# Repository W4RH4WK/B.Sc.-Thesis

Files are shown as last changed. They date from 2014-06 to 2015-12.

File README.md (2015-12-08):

# Improved On-Board Communication for Low-Cost Mobile Robots

This project seeks to improve the communication process between the host
computer of an existing, low-cost robot, and some on-board peripherals. This
robot is used by the department of Computer Science at University of Innsbruck
for teaching students autonomous systems. The robot is driven by an Android
phone which communicates with the robot’s internal peripherals. The components
in use for this communication process introduce various problems which are
resolved by this project to ensure better user experience.

Possible prototypes have been evaluated to find the best possible solution for
the task. Although the best solution still has some flaws, another prototype
was created which brings some new benefits along. Among them are easy to use
and easy to maintain interfaces. Together with the prototypes documentation and
examples have been crafted to ensure easy access to the material for students.
Modularity of the robot has been improved which enables other people to easily
enhance the robots capabilities.

The component used in the final solution consists of a microcontroller which is
programmed to read in data from an Android phone and controls the robot
accordingly. Apart from hardware the microcontroller’s firmware has been
written together with and example Android application.

## Known Issues

- `2015-04-30` Since the firmware's command buffer logic ignores `\r` (carriage
  return) and terminates on `\n` (linefeed), one cannot use the corresponding
  values as arguments. Just increment the value by one before sending, you
  won't notice the difference anyway.

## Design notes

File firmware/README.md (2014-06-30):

# FT232 AVR Program

This code will run on the ATmega32 AVR located on FT232 v0.X boards. A simple
Makefile is provided to build and flash this program and to setup the fuses
properly.

## Modules
- `command` defines a buffer and logic for command execution
- `config`  contains global configuration
- `log`     defines a `log()` macro
- `robot`   contains all robot related functions
- `timer1`  helper for timer 1
- `twi`     helper for two wire interface (I2C)
- `uart`    helper functions, UART stream, UART receive interrupt

## Commands
Have a look at `command.c`, the `command_exec` function contains all available
commands and their code.

A command is issued as multiple bytes send to the controller over UART. The
first byte will determine the command, following bytes are treated as arguments
for the selected command. Commands are terminated with `\n`. `\r` will be
ignored to prevent double execution on `\r\n`.

Sensor-data and similar information will be written back as simple strings
terminated with `LINE_ENDING` defined in `config.h`.

This setup enables the user to communicate with the controller using a simple
terminal application like minicom or putty. Some of these applications require
you to hit CTRL + J to send a `\n`, RETURN will only send `\r`.

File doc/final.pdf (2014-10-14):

## Improved On-Board Communication for Low-Cost Mobile Robots

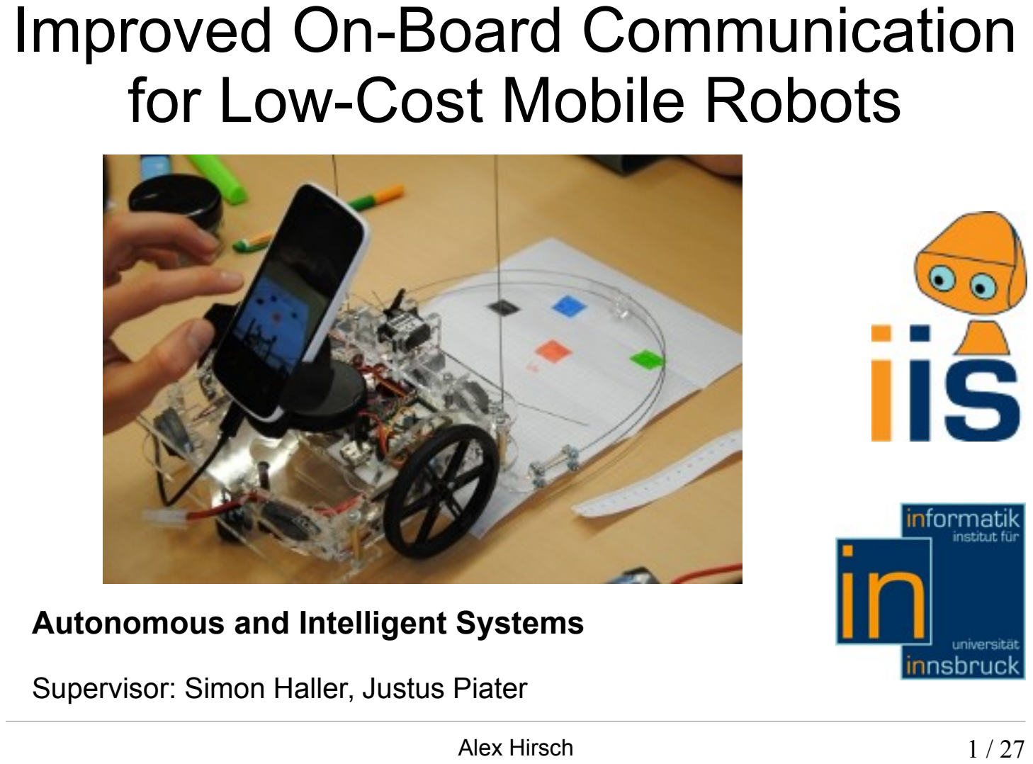
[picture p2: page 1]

Alex Hirsch | 1 / 27

Autonomous and Intelligent Systems

Supervisor: Simon Haller, Justus Piater

## Content

- Problems / Goals
- The Robot
- Possible Solutions / Evaluation
- FT311D
- Atmega32
- Android App

## My Experience (Summer 2013)

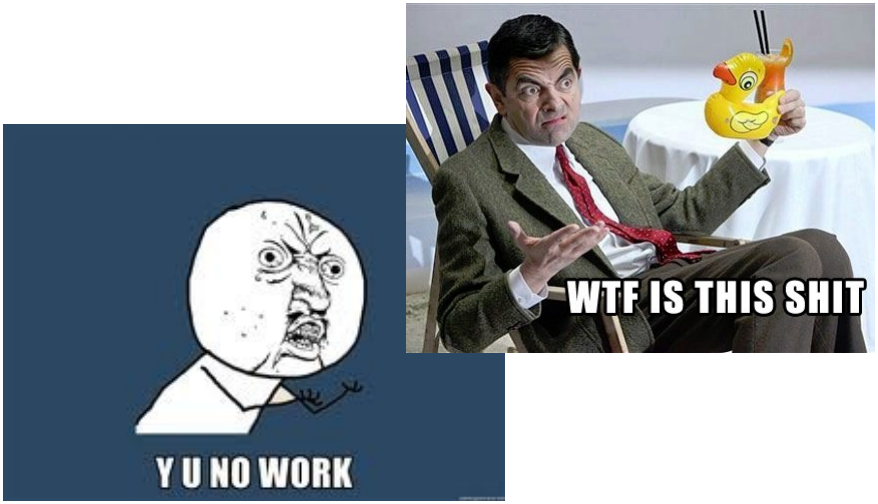
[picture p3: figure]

## Problems

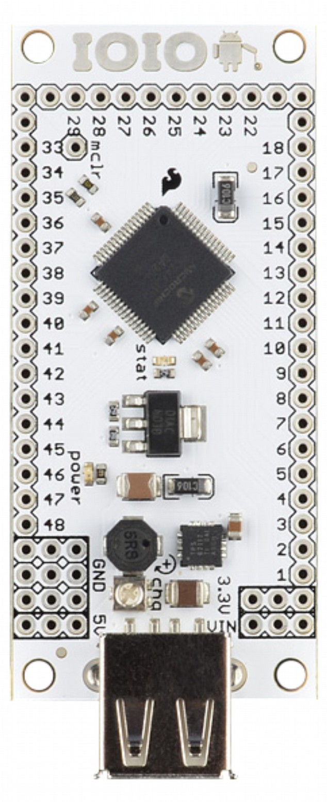
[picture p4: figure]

- far too complex for
communication
- Multi-threaded
connection
- depends on Android
Version

## Goals

- improved communications (new hardware)
- code examples
- none multi-threaded Android interface
- easy to use
- good documentation
- forward-compatible

## The Robot

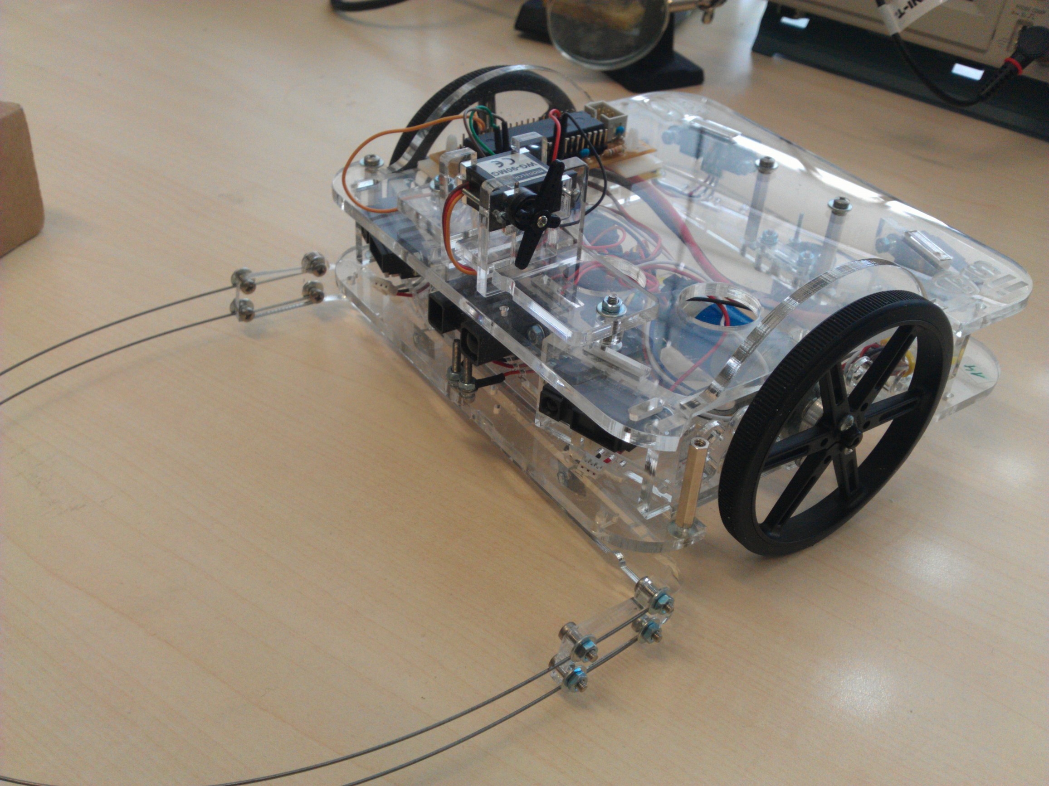
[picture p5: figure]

## 2 Layers

Interior

- DC Motors
- IR Sensors
- Control Board
- Battery

On Top

- Comm Board
- Servo Motor
(Catching Balls)

## Interior

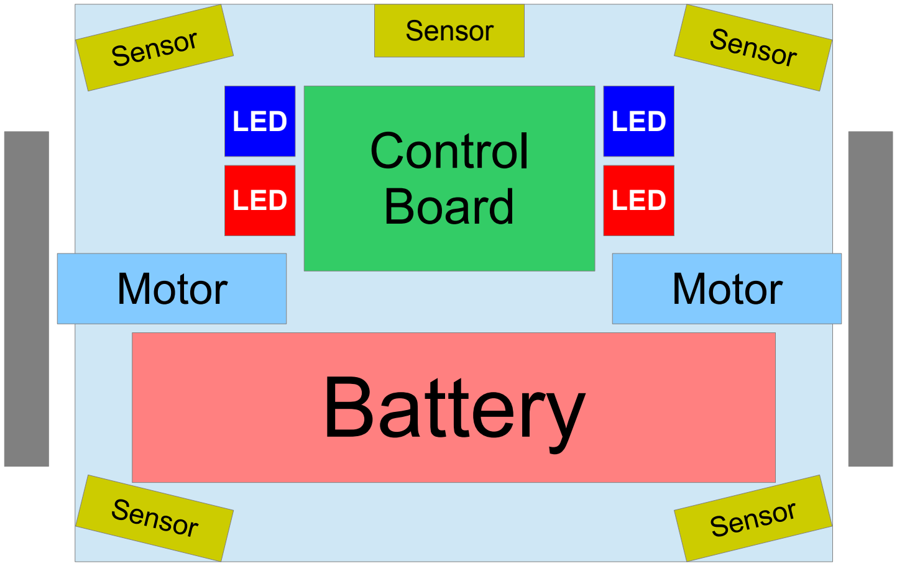
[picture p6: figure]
Battery; Control Board; Motor; Sensor; Sen; sor; LED

## On Top

Servo
Motor

Comm
Board

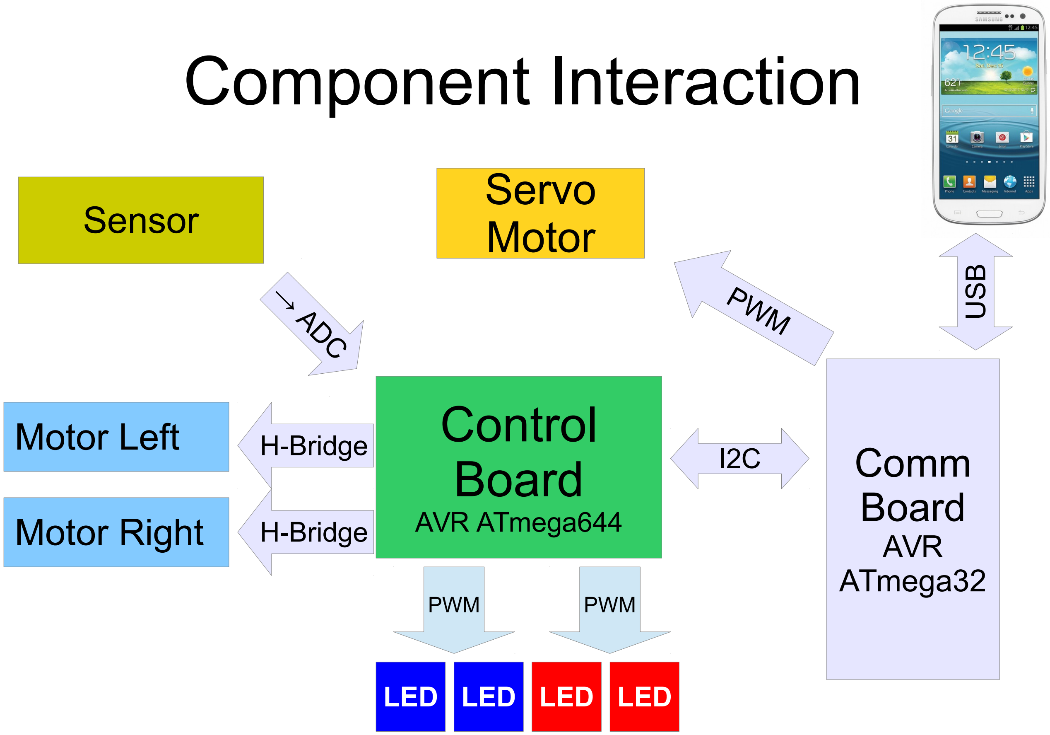
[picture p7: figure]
Component Interaction; Comm Board AVR ATmega32; PWM; Servo Motor; Control Board; AVR ATmega644; Motor Right; Motor Left; H-Bridge; Sensor; → ADC; LED

## Evaluation

- Cost cheap components since multiple robots have to be equipped
- Simplicity easy to build, maintain and use
- Availability required components must be available
- Modularity keep or enhance present modularity
- Future Oriented keep forward compatibility to ensure robustness

## Candidates

- FT311D
- Arduino Uno
- Raspberry Pi (Model B)
- Beagle Bone Black
- ATmega 32 AVR

## Evaluation Result

Candidate | Cost | Simplicity | Availability | Modularity | Future Oriented | Total
FT311D | 5 | 5 | 5 | 4 | 3 | 22
ATmega 32 | 4 | 3 | 5 | 5 | 4 | 21
Arduino Uno | 3 | 3 | 4 | 4 | 3 | 17
Raspberry Pi | 2 | 2 | 4 | 3 | 4 | 15
Beagle Bone | 1 | 1 | 2 | 3 | 4 | 11

1 – 5 points per category

higher is better

## USB Mode: Host + Accessory

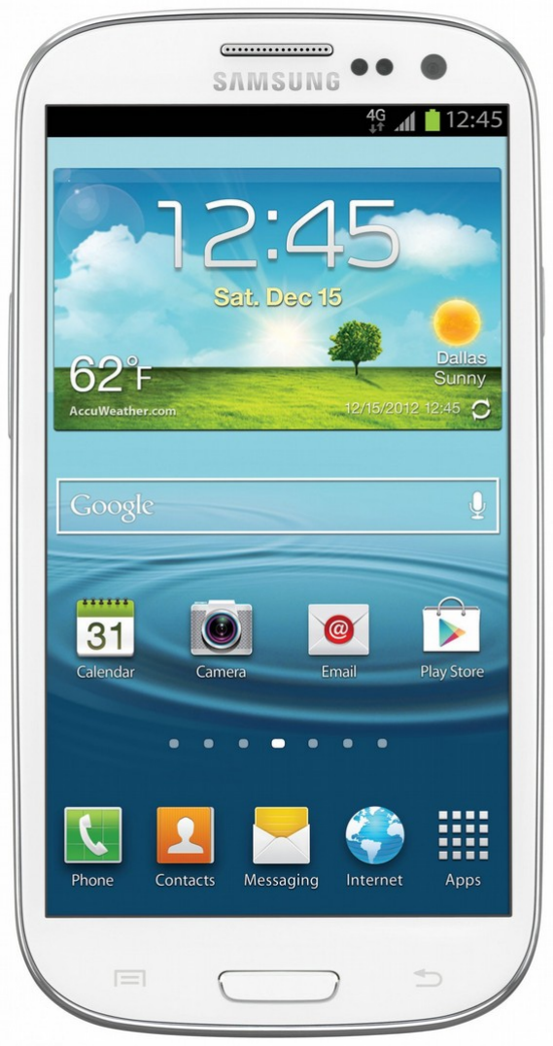
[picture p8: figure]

USB

Host | Accessory

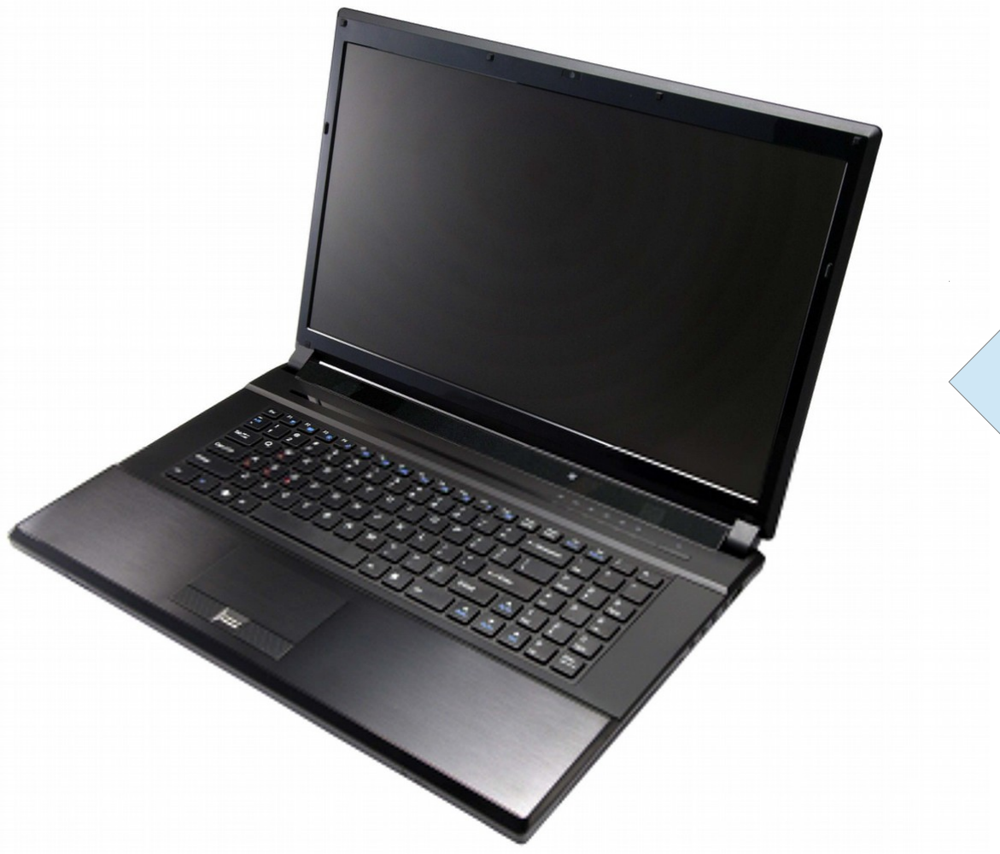
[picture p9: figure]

- requires driver
- Host has to recognize Accessory

## USB Mode: On-The-Go (OTG)

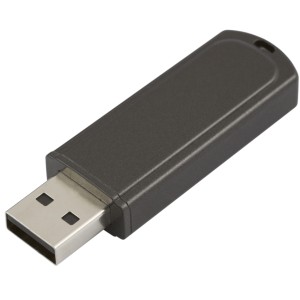
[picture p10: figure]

USB

Host

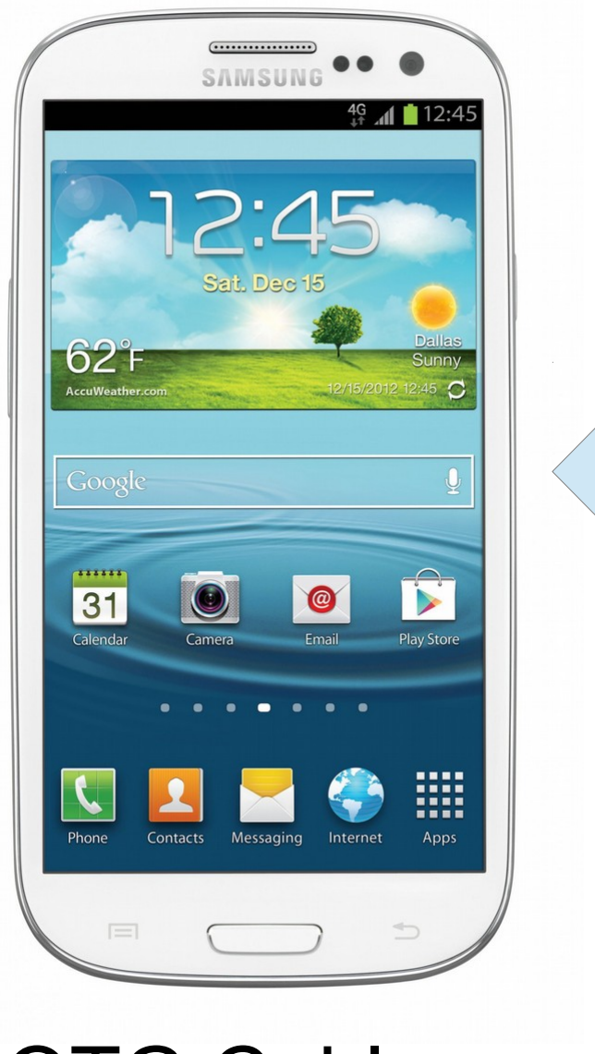
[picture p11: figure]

- Requires OTG Cable
- Not all Android phones support OTG

Accessory

## USB OTG (on the go)

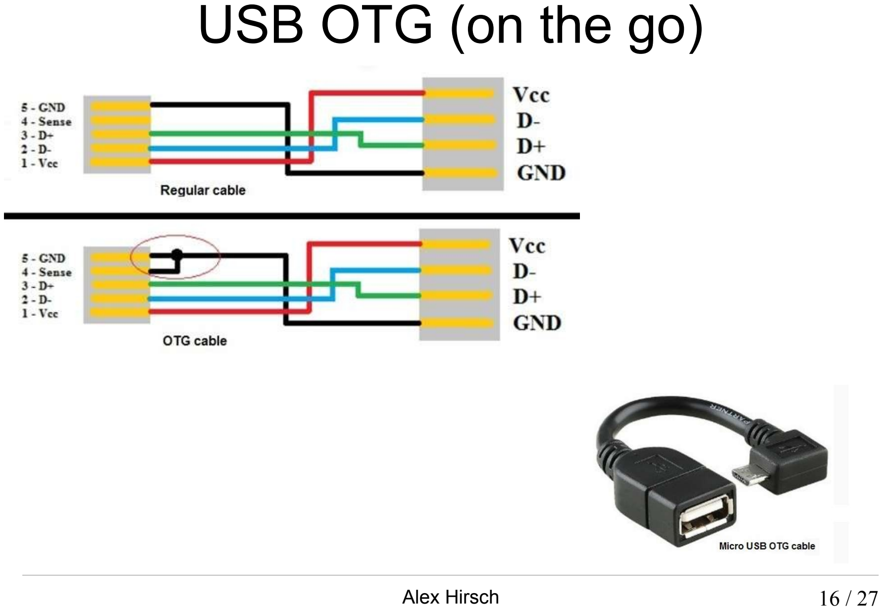
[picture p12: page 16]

## FT311D Prototype

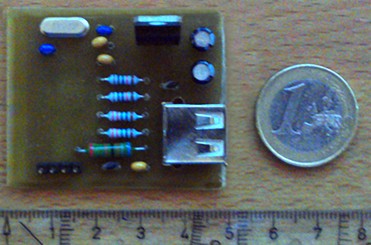
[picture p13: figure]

## FT311D Prototype

- no programming required
- simple converter
- provides different interfaces (UART, SPI, I2C, ...)
- Depends on Android Version

## ATmega 32 Prototype

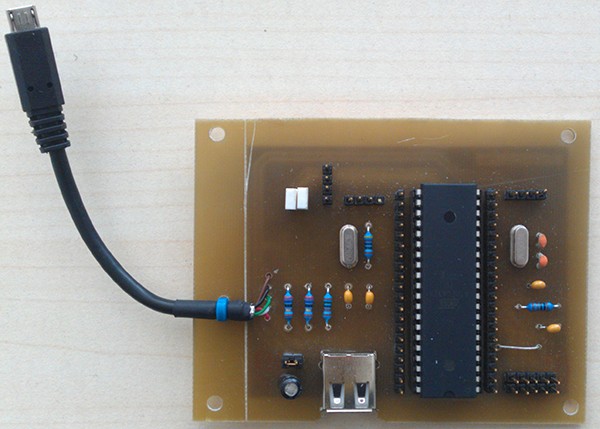
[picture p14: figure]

## ATmega 32 Prototype

- programmable
- has useful hardware peripherals
- more than just a converter
- good documentation
- not capable of USB handling
requires simple USB to serial converter

## Communication (wired)

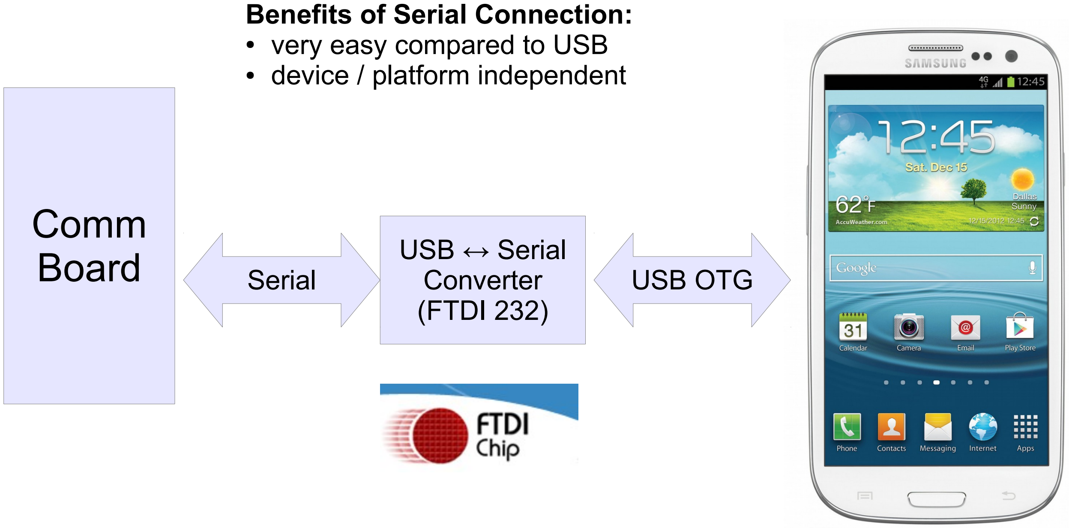
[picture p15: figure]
Comm; Board; USB OTG; USB ↔ Serial Converter (FTDI 232); Serial; Benefits of Serial Connection: ● very easy compared to USB ● device / platform independent

## Communication (wireless)

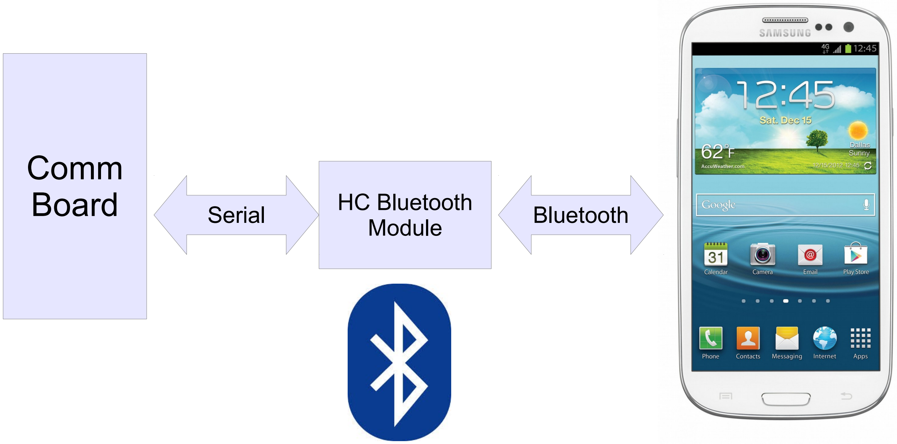
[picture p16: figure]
Comm; Board; Bluetooth HC Bluetooth; Module Serial

## Final Board

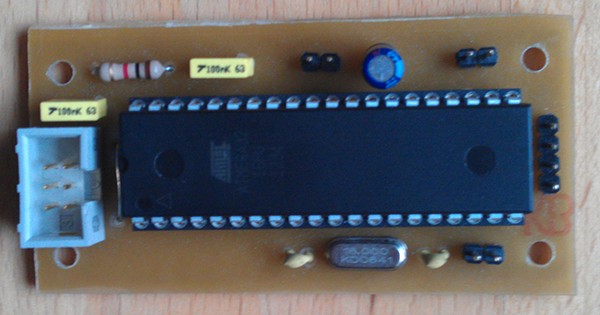
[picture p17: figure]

## USB to serial Converter

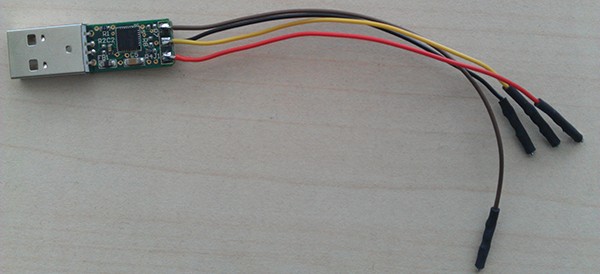
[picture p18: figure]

## Android App

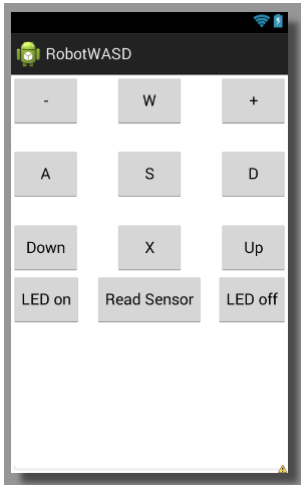
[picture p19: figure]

- Move robot
- Toggle LEDs
- Read in sensor data
- Move cage

## Future

- Combine CommBoard and ControlBoard
- Replace Android phone with embedded system
- Improve the robot's casing

Questions?

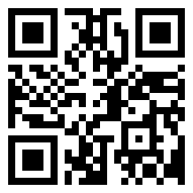
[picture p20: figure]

source code:

http://git.io/wVlDzg

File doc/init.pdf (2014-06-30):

## Improved On-Board Communication for Low-Cost Mobile Robots

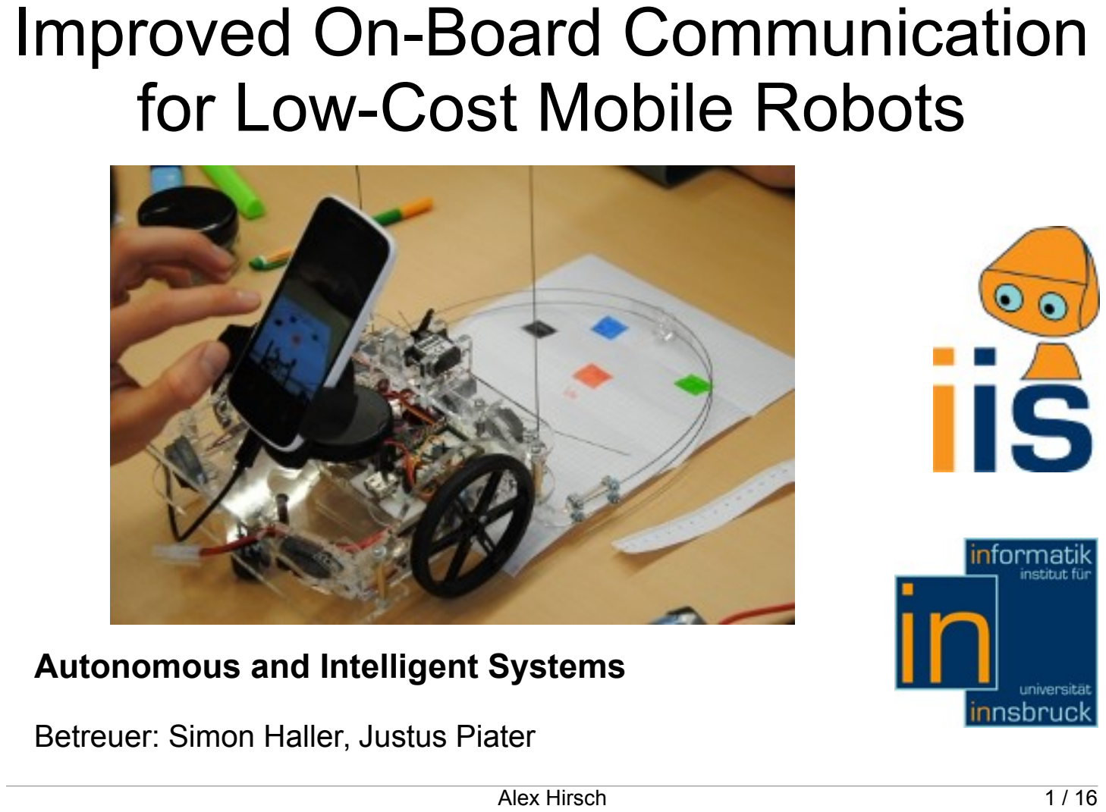
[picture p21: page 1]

Alex Hirsch | 1 / 16

Autonomous and Intelligent Systems

Betreuer: Simon Haller, Justus Piater

## Robot Internals

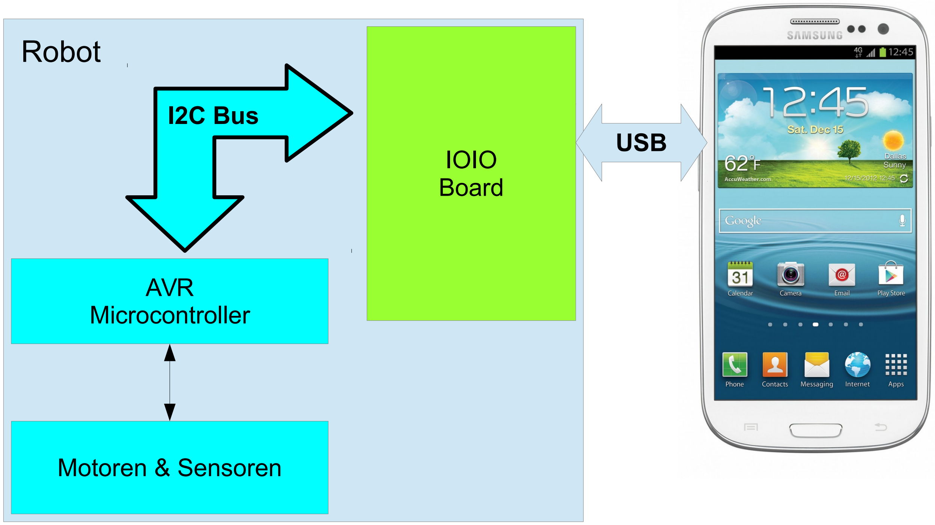
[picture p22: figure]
Robot; Motoren & Sensoren; AVR Microcontroller; IOIO Board; I2C Bus; USB

## USB Mode: Host + Accessory


USB

Host | Accessory


- Benötigt meist Treiber
- Host muss Accessory richtig erkennen

## USB Mode: On-The-Go (OTG)


USB

Host

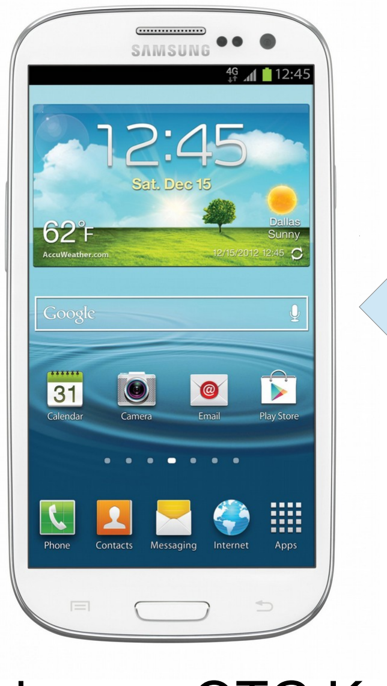
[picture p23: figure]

- Benötigt eigenes OTG Kabel
- Nicht jedes Android Phone kann OTG

Accessory

## USB OTG Kabel

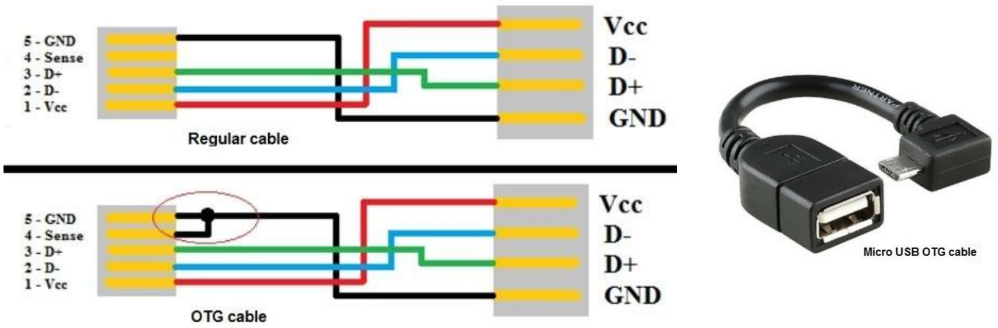
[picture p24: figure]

- Geringe Kosten
- Lieferbar

## IOIO Board (Host + Accessory)

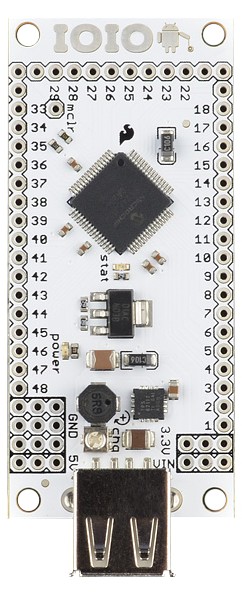
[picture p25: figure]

- Unnötig komplex
- Große API
(Android IOIO Lib)
- Android Versions
Abhängigkeit

Host

## FT311D (Host + Accessory)


- Einfach
- Multifunktional
- Android Versions
Abhängigkeit

Host

## FT232 (On-The-Go)

- Weit verbreitet
(Treiber)
- Simpler USB zu
Serial converter
- Simples Interface

Accessory

## Prozess: Prototyping


## Prozess: Prototyping


## Prozess: Prototyping


## Output

- Neue Kommunikations-Hardware – Erweiterbar
– Versionsunabhängig
- Software Library + Example
- Gute Dokumentation

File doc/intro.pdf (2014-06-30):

# Robot Introduction


Alex Hirsch | 1 / 32

Questions:
alexander.hirsch@student.uibk.ac.at

# Content

# - The Robot (internals + components) - Communication (USB OTG / Bluetooth) - Setup everything - Example App - Details: I2C, H-Bridge, PWM, Sensors

# My Experiance (last year)


# Now Better (hopefully)

# - Improved communications - Code examples - Knowledge about firmware / interior setup - Not multithreaded (better debugging) - Easy to use interface

# The Robot


# 2 Layers

# Interior - DC Motors (movement) - IR Sensors (range detection) - Control Board - Battery

# On Top - Comm Board

# → new ←

# - Servo Motor (Catching Balls)

# Interior

Battery; Control Board; Motor; Sensor; Sen; sor; LED

# On Top

## Servo Motor

## Comm Board

# Component Interaction

Comm Board; Servo Motor; Control Board; Motor Right; Motor Left; Sensor; LED

# Component Interaction (detail)

Comm Board AVR ATmega32; PWM; Servo Motor; Control Board; AVR ATmega644; Motor Right; Motor Left; H-Bridge; Sensor; → ADC; LED

# Communication (wired)

Comm; Board; USB OTG; USB ↔ Serial Converter (FTDI 232); Serial; Benefits of Serial Connection: ● very easy compared to USB ● device / platform independent; Code Examples Provided, scroll down

Phone powers Converter + Comm Board

# USB OTG (on the go)


# Communication (wireless)

Comm; Board; Bluetooth HC Bluetooth; Module Serial; Code Examples → Google; Pair w/ Phone Secret code: 1234; Comm Board Powers Bluetooth module

Serial Convert
/
Bluetooth

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
V (o

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
ol B

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
ol B

o

a

r

d


S
e
rv
o

N
C

NC … not connected

+5V
Ground
RxD
TxD

# Setup everything up

# 1) Make sure Comm Board is connected propperly 2) Connect serial converter / Bluetooth module to Comm Board 3) Check if battery is connected 4) Push button on the underside of the Robot 5) Connect Phone

# Sneaky Button: On / Off


# How does Serial Work

Device 1 | Device 2

RxD

TxD | RxD TxD

Parameters:
Speed (Baud): 9600
Data bits: 8
Stop bits: 1
No Parity
No Flow control

Detail:
Same as RS232
but with 0V 5V | It's character based!

# WASD example App


W | Move forward
S | Stop
A | Turn left
D | Turn right
X | Move backward
- Lower bar a few degree
+ | Rise bar a few degree
Down | Fixed position for bar (low)
Up | Fixed position for bar (high)

Debug Output + Sensor Data Below

Application needs FTDriver library https://github.com/ksksue/FTDriver

# WASD Code FTDriver instance

private FTDriver com;

@Override
protected void onCreate(Bundle savedInstanceState) { super.onCreate(savedInstanceState); setContentView(R.layout.activity_main);

textLog = (TextView) findViewById(R.id.textLog);

com = new FTDriver((UsbManager) getSystemService(USB_SERVICE));

connect();
}

# WASD Code Write Data

private FTDriver com;

public void comWrite(byte[] data) { if (com.isConnected()) {
com.write(data);
} else {
textLog.append("not connected\n"); }
}

# WASD Code Read Data

private FTDriver com;

public String comRead() {
String s = "";
int i = 0;
int n = 0;
while (i < 3 || n > 0) {
byte[] buffer = new byte[256]; n = com.read(buffer);
s += new String(buffer, 0, n); i++;
}
return s;
}


Strange android tripple buffering

# WASD Code ReadWrite Data

private FTDriver com;

public String comReadWrite(byte[] data) { com.write(data);
try {
Thread.sleep(100);
} catch (InterruptedException e) { // ignore
}
return comRead();
}

# WASD Code Commands

\r is ignored anyway, \n is used as lineending

w | Move forward
s | Stop
a | Turn left
d | Turn right
x | Move backward
- Lower bar a few degree
+ | Rise bar a few degree
r | LEDs on
e | LEDs off
q | Read sensors
Commands without parameter | Commands with parameter
| public void robotSetLeds(byte red, byte blue)
{
| ComReadWrite( new byte[] { 'u', red, blue, '\r', '\n' } );

}

| public void robotSetVelocity(byte left, byte right) { ComReadWrite( new byte[] { 'i', left, right, '\r', '\n' } );

}

| public void robotSetBar(byte value) { ComReadWrite( new byte[] { 'o', value, '\r', '\n' } );

}
Example:
new byte[] {'w', '\r', '\n'};

# Android USB Permission (simple)

<?xml version="1.0" encoding="utf-8"?>
<manifest ...>
<uses-feature android:name="android.hardware.usb.host" /> <application ...>
<activity ...>
<intent-filter>
<action android:name="android.intent.action.MAIN" />
<category android:name="android.intent.category.LAUNCHER" /> <action
android:name="android.hardware.usb.action.USB_DEVICE_ATTACHED" /> </intent-filter>
<meta-data
android:name="android.hardware.usb.action.USB_DEVICE_ATTACHED" android:resource="@xml/device_filter" />
</activity>
</application>
</manifest>

# Android USB Permission (better)

# - Use intent filter

+

# - Implement Permission request

see https://developer.android.com/guide/topics/connectivity/usb/host.html

# Bluetooth

## - see http://luugiathuy.com/2011/02/android-java-bluetooth/ - see http://english.cxem.net/arduino/arduino5.php


# I2C Communication


Src: ATmega32 datasheet

Master / Slave
Each slave has a 7 Bit address
+ 1 bit to state read or write access

# I2C Communication (example)


# LEDs (PWM)


PWM... Pulse Width Modulation

# DC Motors (H - Bridge)


VNH3SP30-E

PWM is used to determine
velocity

# IR Sensor


GP2Y0A21YK0F
According to Datasheet
from 10 to 80 cm


Sensor Output Voltage will be provided via the Comm Board in hexadecimal notation (0x00 – 0xFF) per sensor.
Example: “sensor: 0x00 0xa2 0xef 0x12 0xf3 0x01 0x00 0x17”

# Comm Board Code

File | Content
main.c | entry point + command execution
uart.c | serial communication (low level)
twi.c | i2c communication
timer1.c | PWM servo output
log.h | debug macro
command.c | handle received data (available commands listed here)
robot.c | robot control (high level)

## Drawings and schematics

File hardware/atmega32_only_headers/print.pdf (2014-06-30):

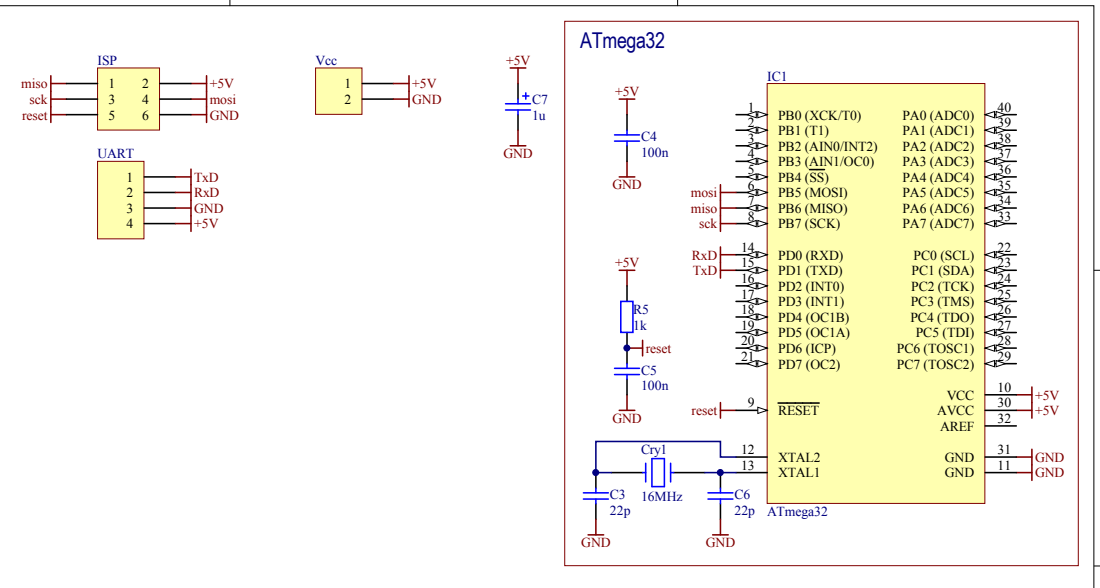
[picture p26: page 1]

ATmega32 final (full pin headers) Alexander Hirsch

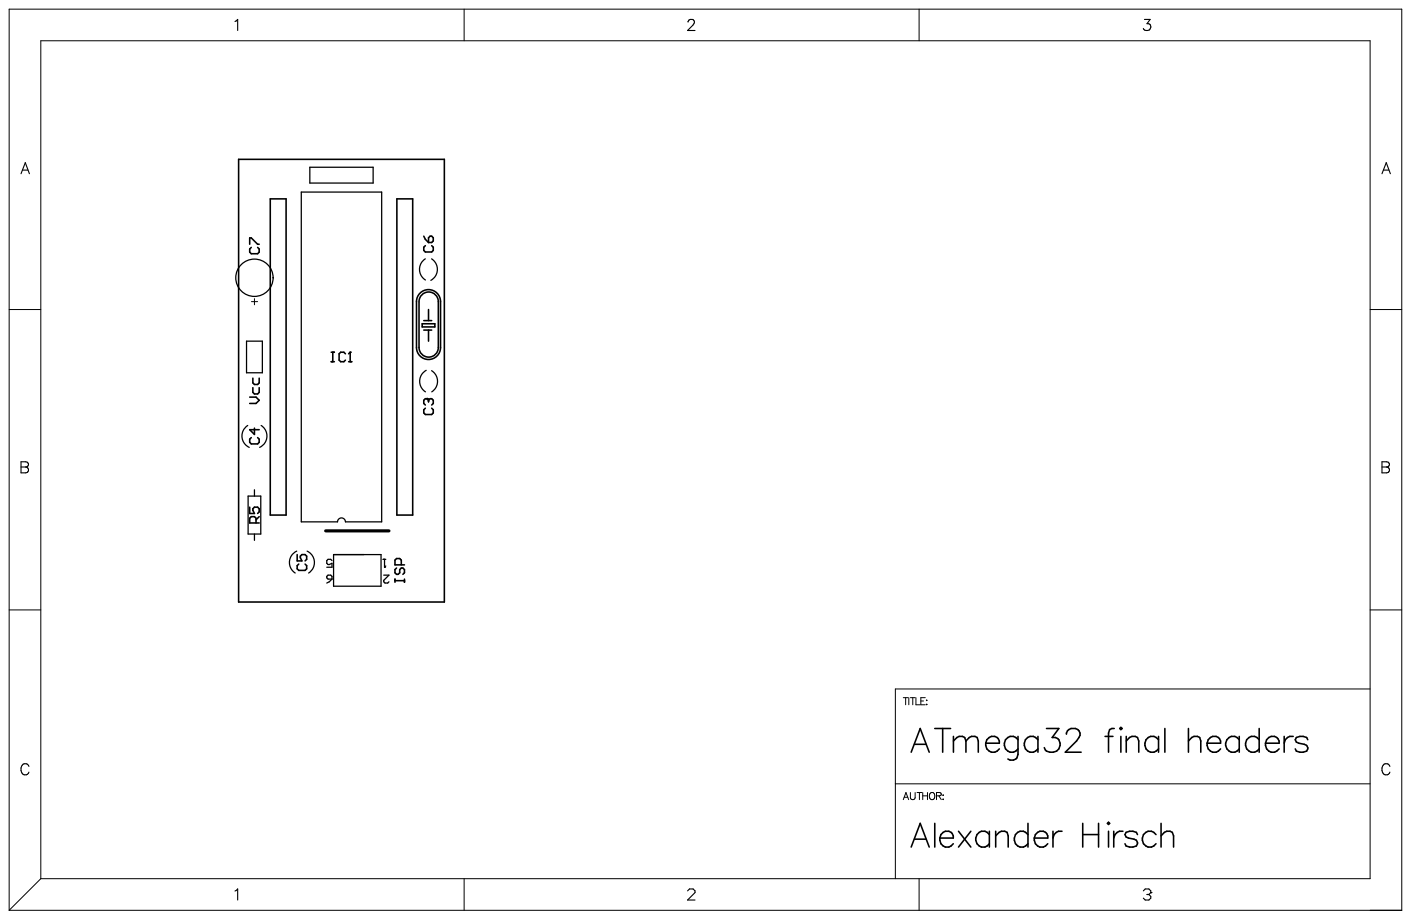
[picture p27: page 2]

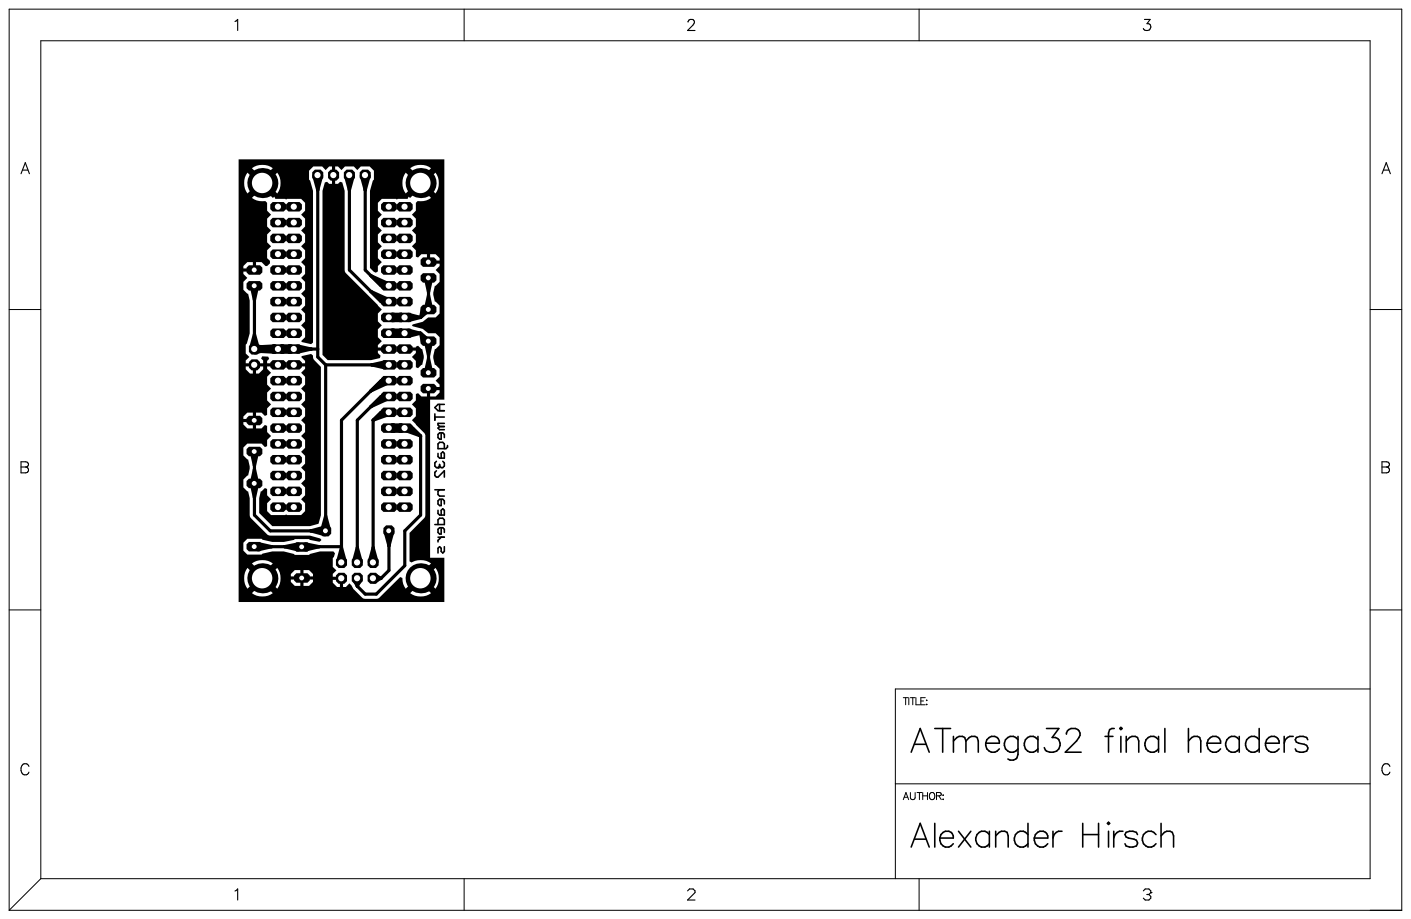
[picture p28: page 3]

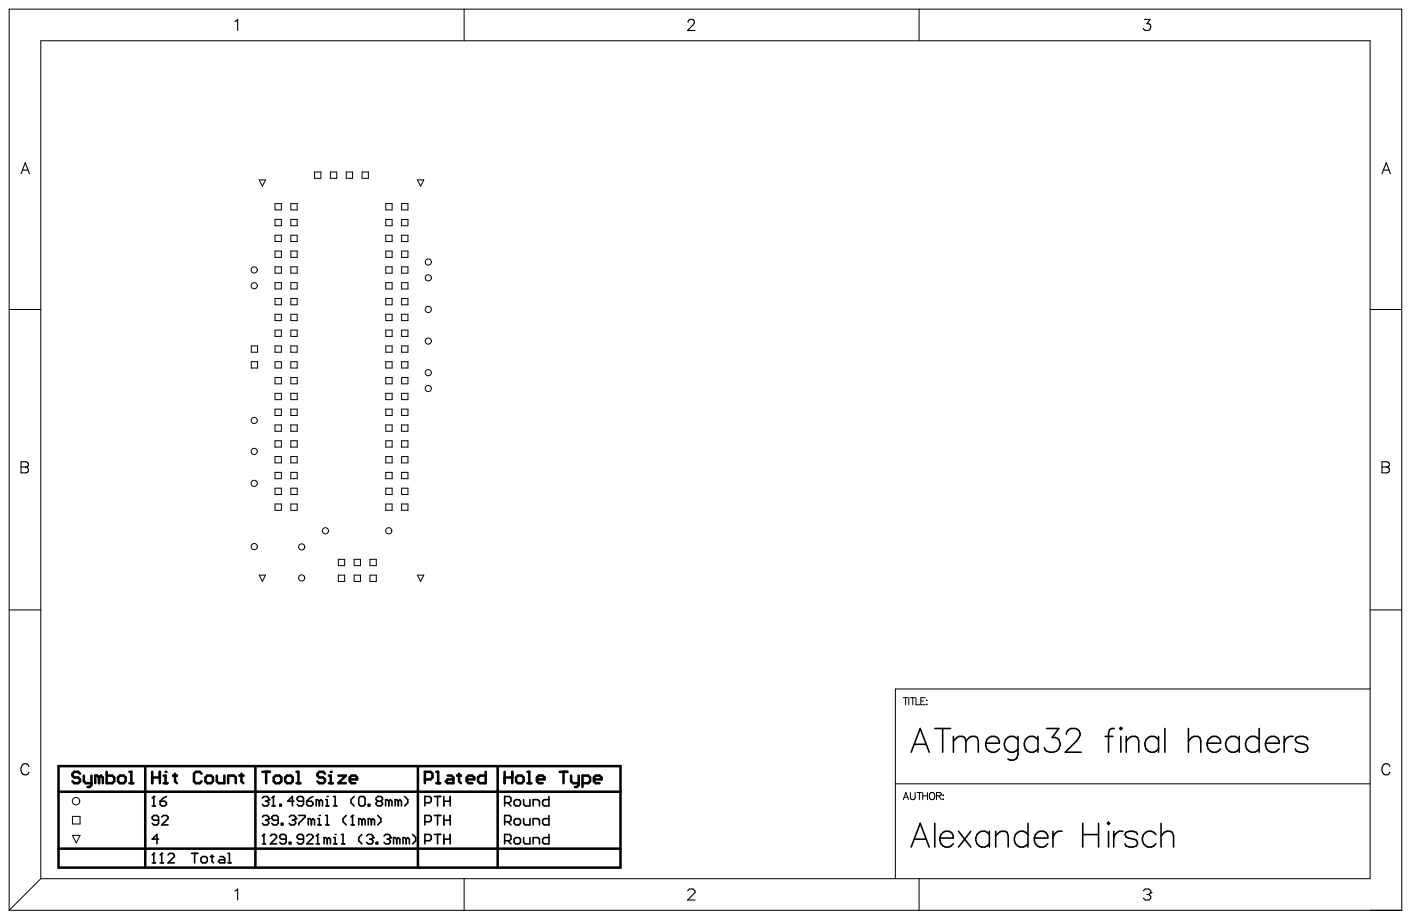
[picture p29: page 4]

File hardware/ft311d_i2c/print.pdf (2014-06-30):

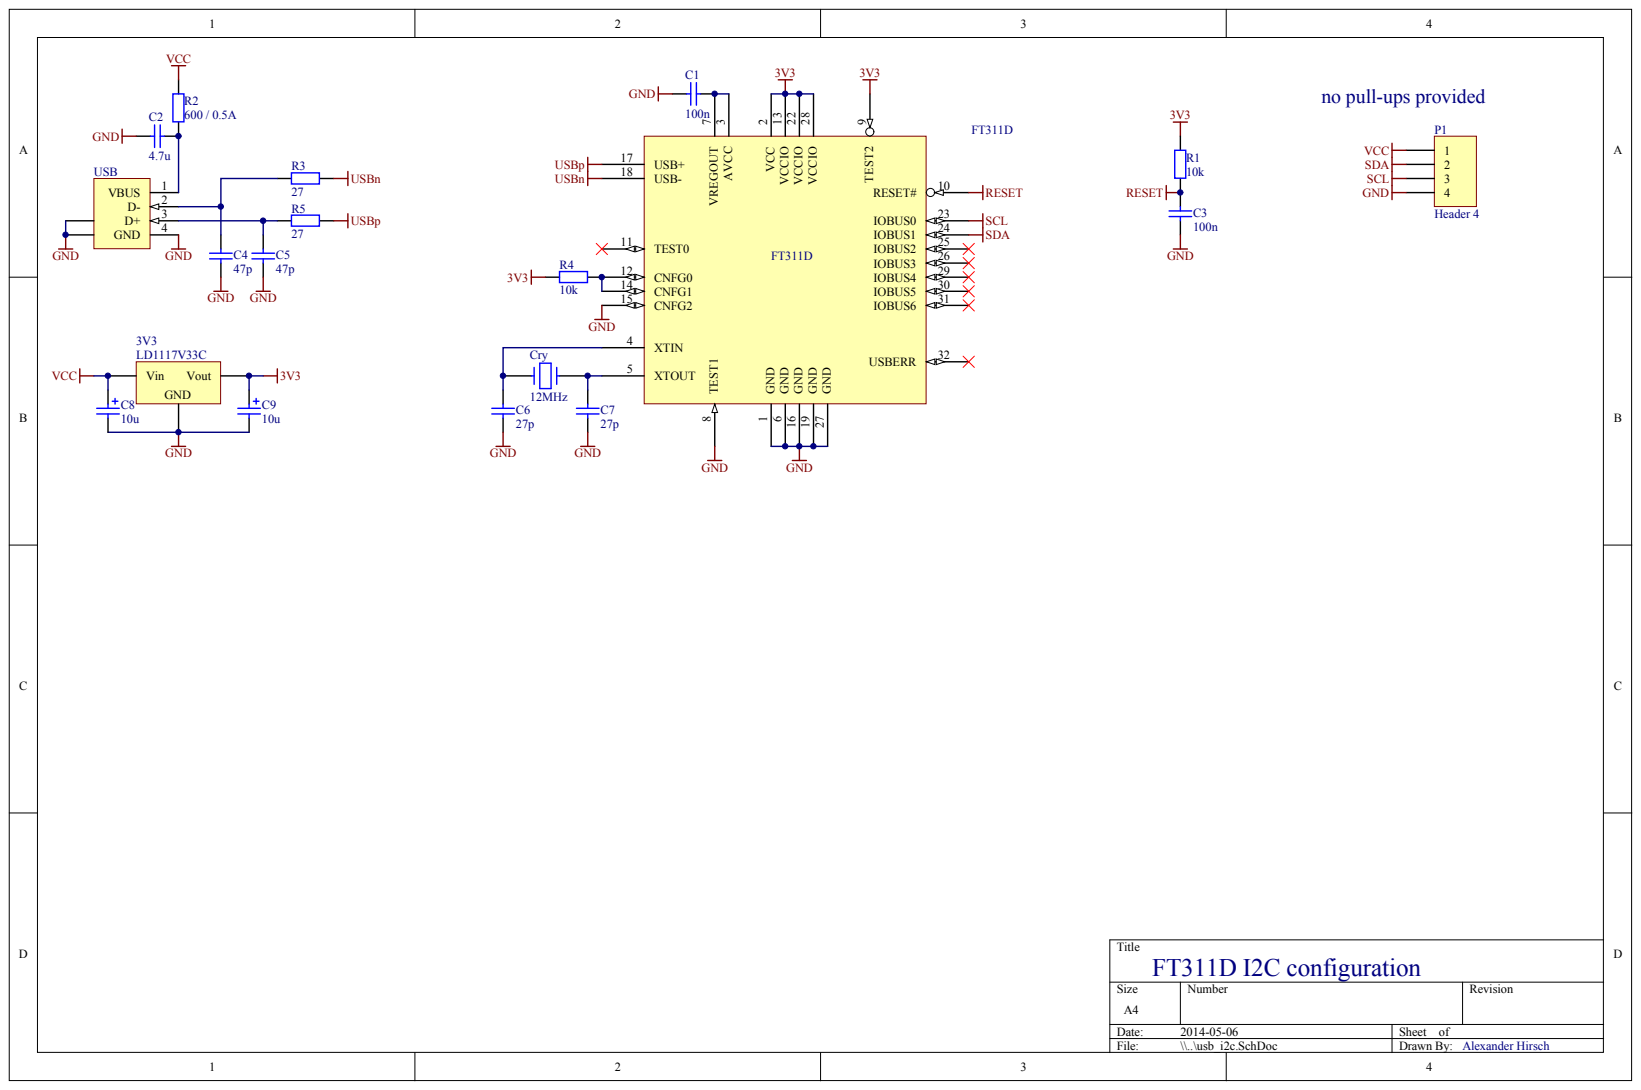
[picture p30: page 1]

no pull-ups provide

GND VCC SDA SCL

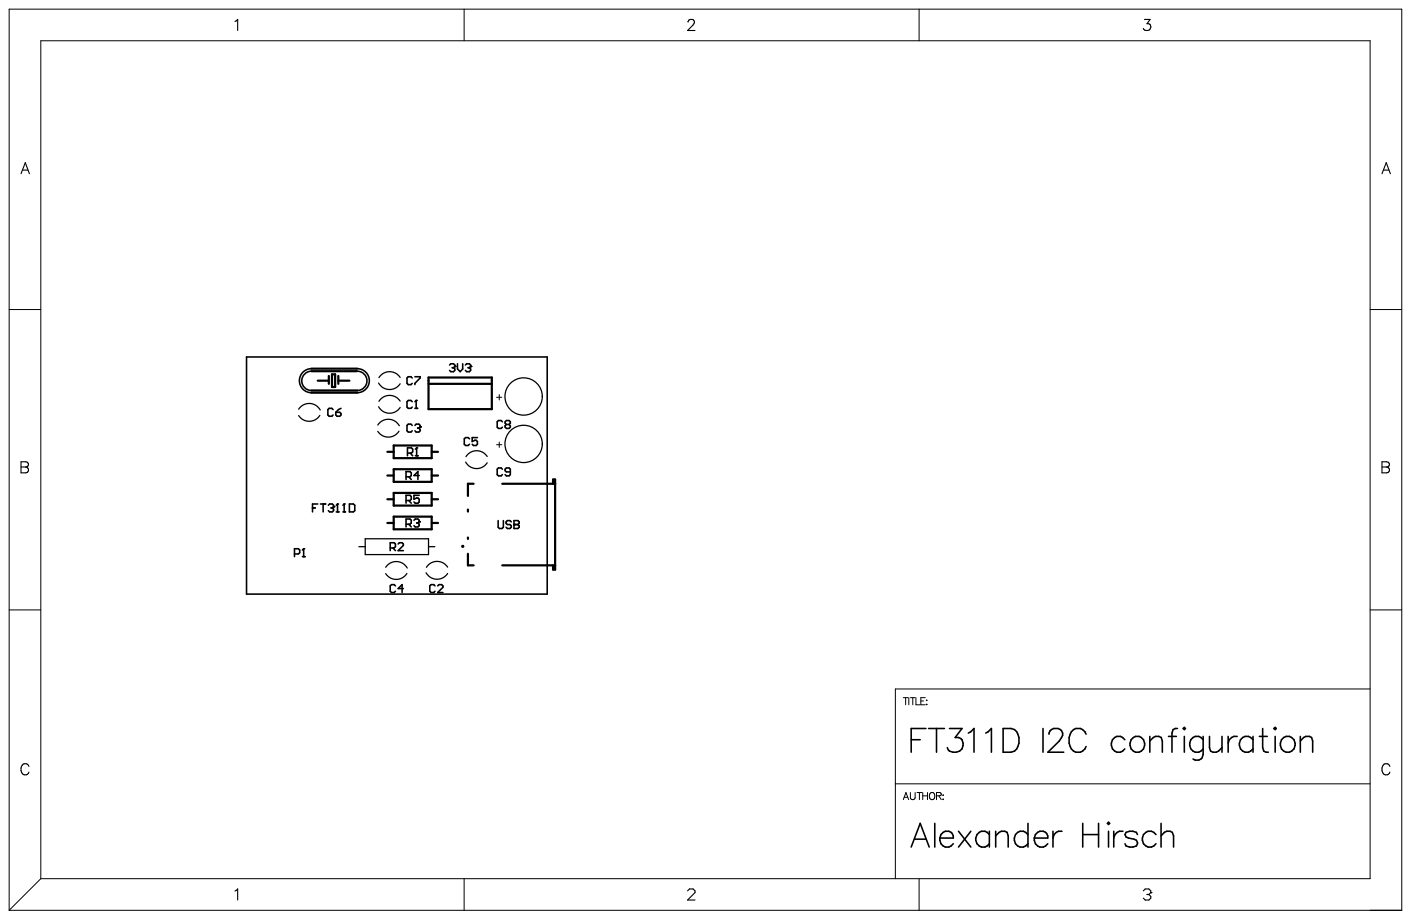
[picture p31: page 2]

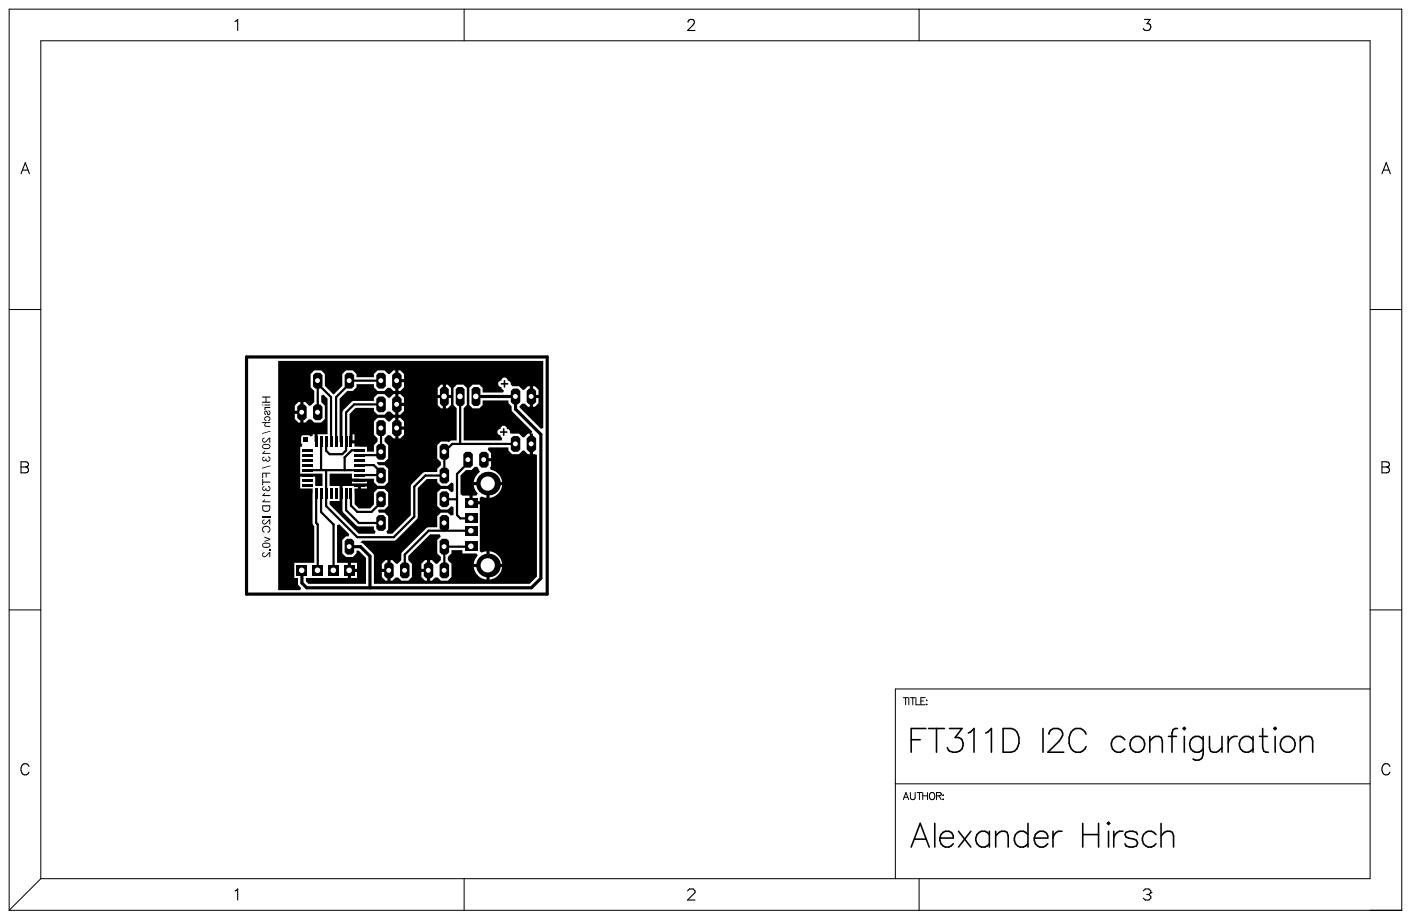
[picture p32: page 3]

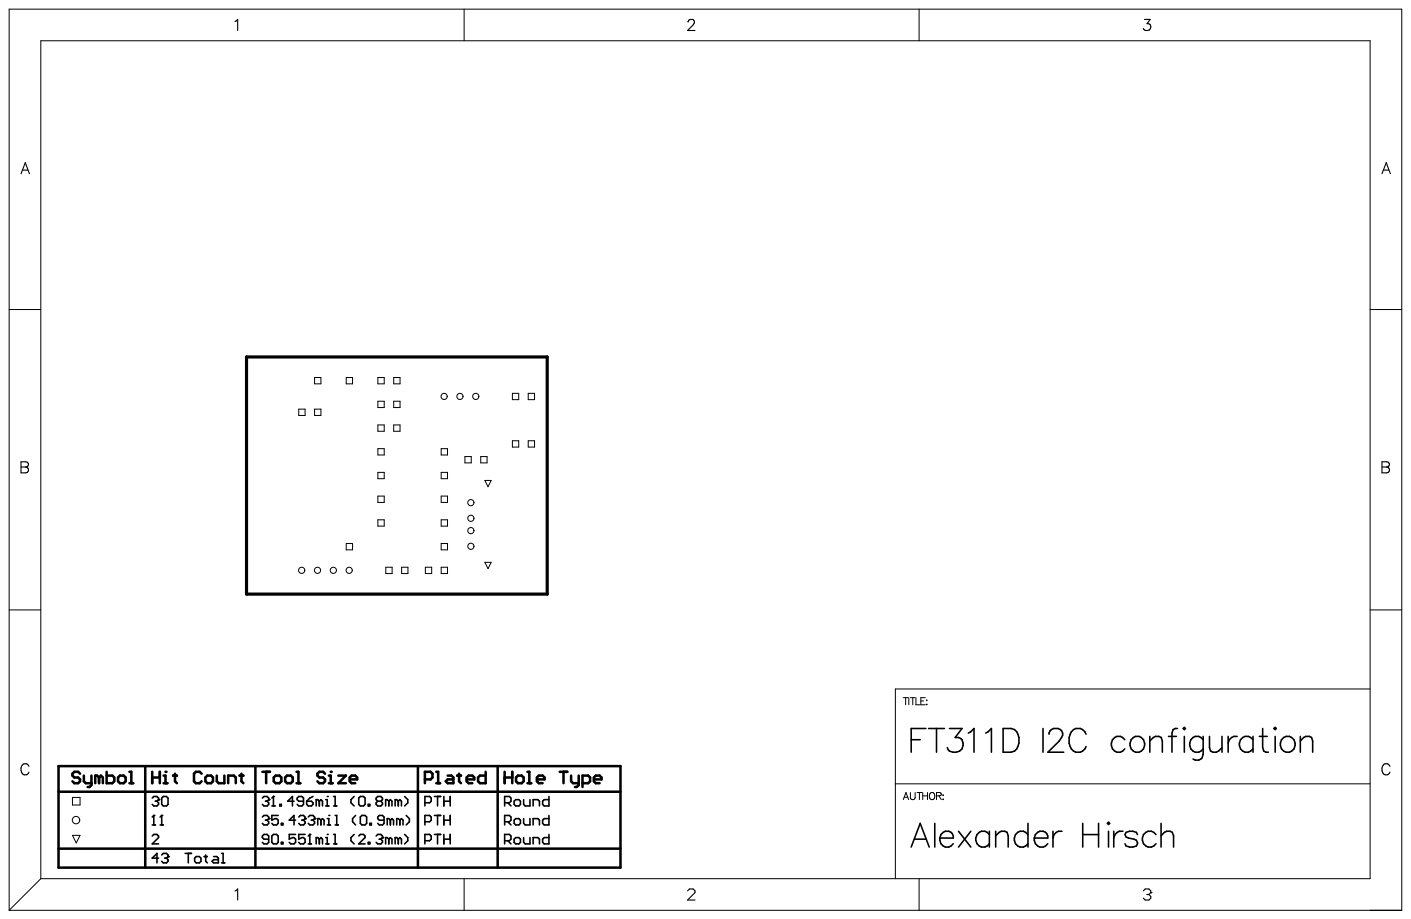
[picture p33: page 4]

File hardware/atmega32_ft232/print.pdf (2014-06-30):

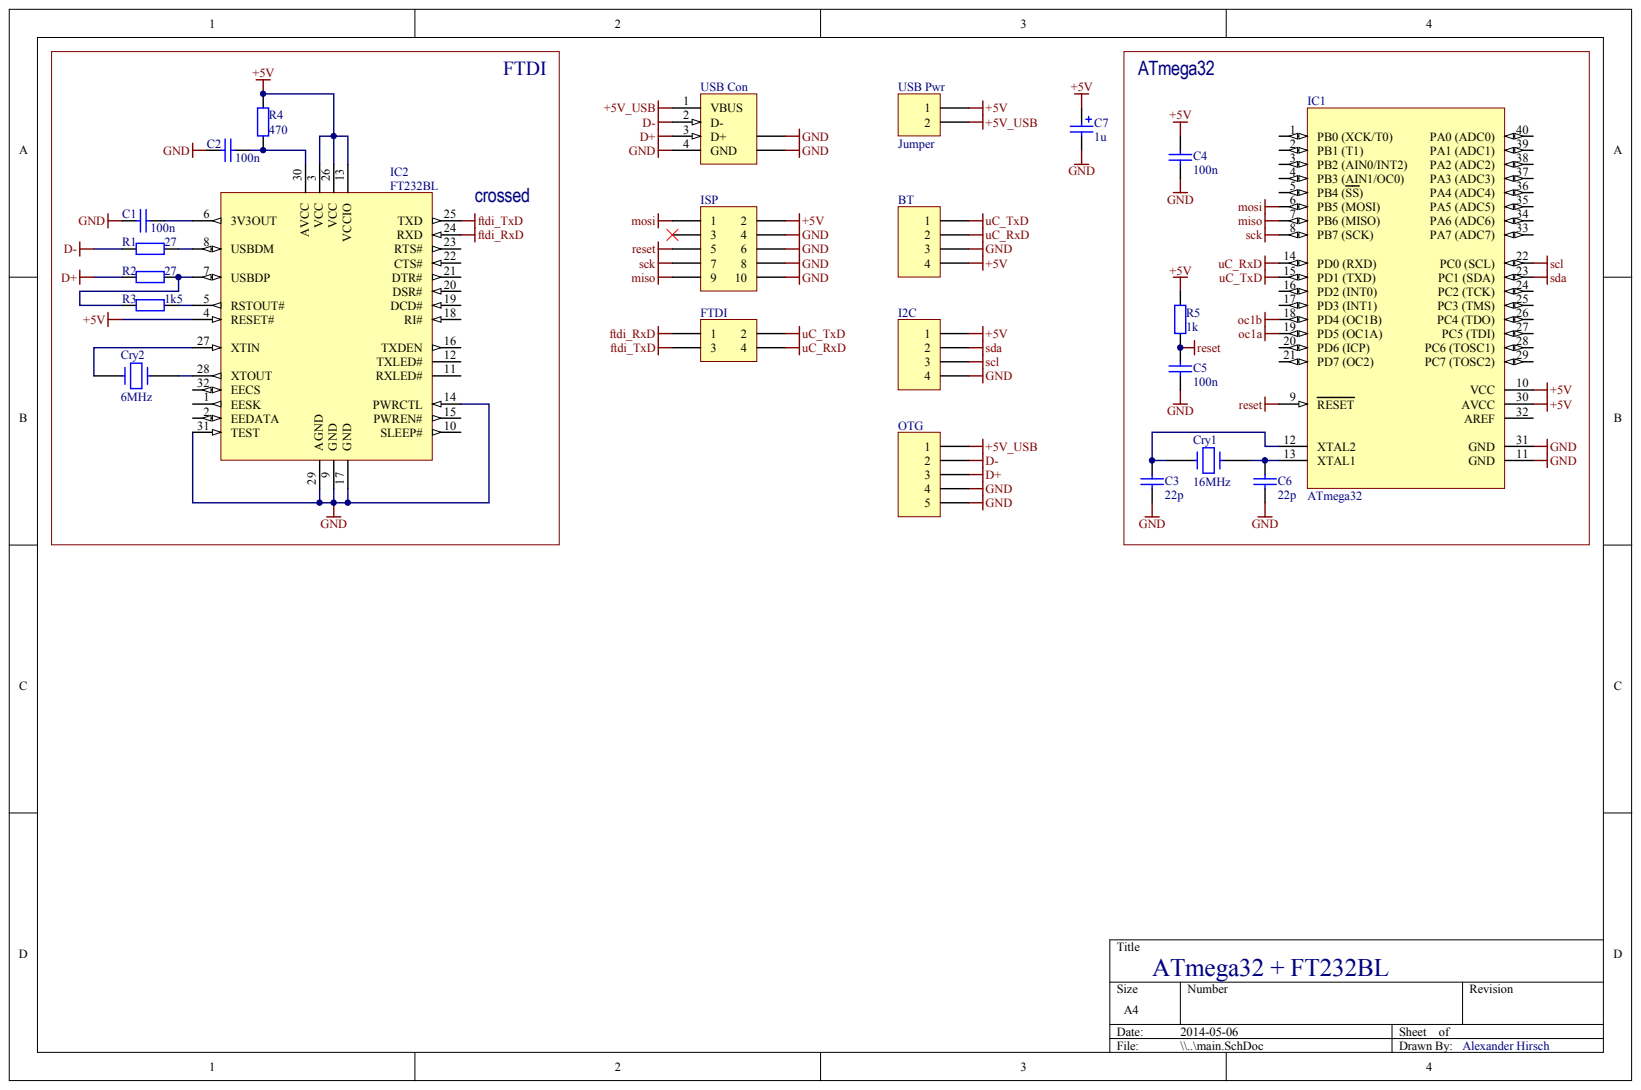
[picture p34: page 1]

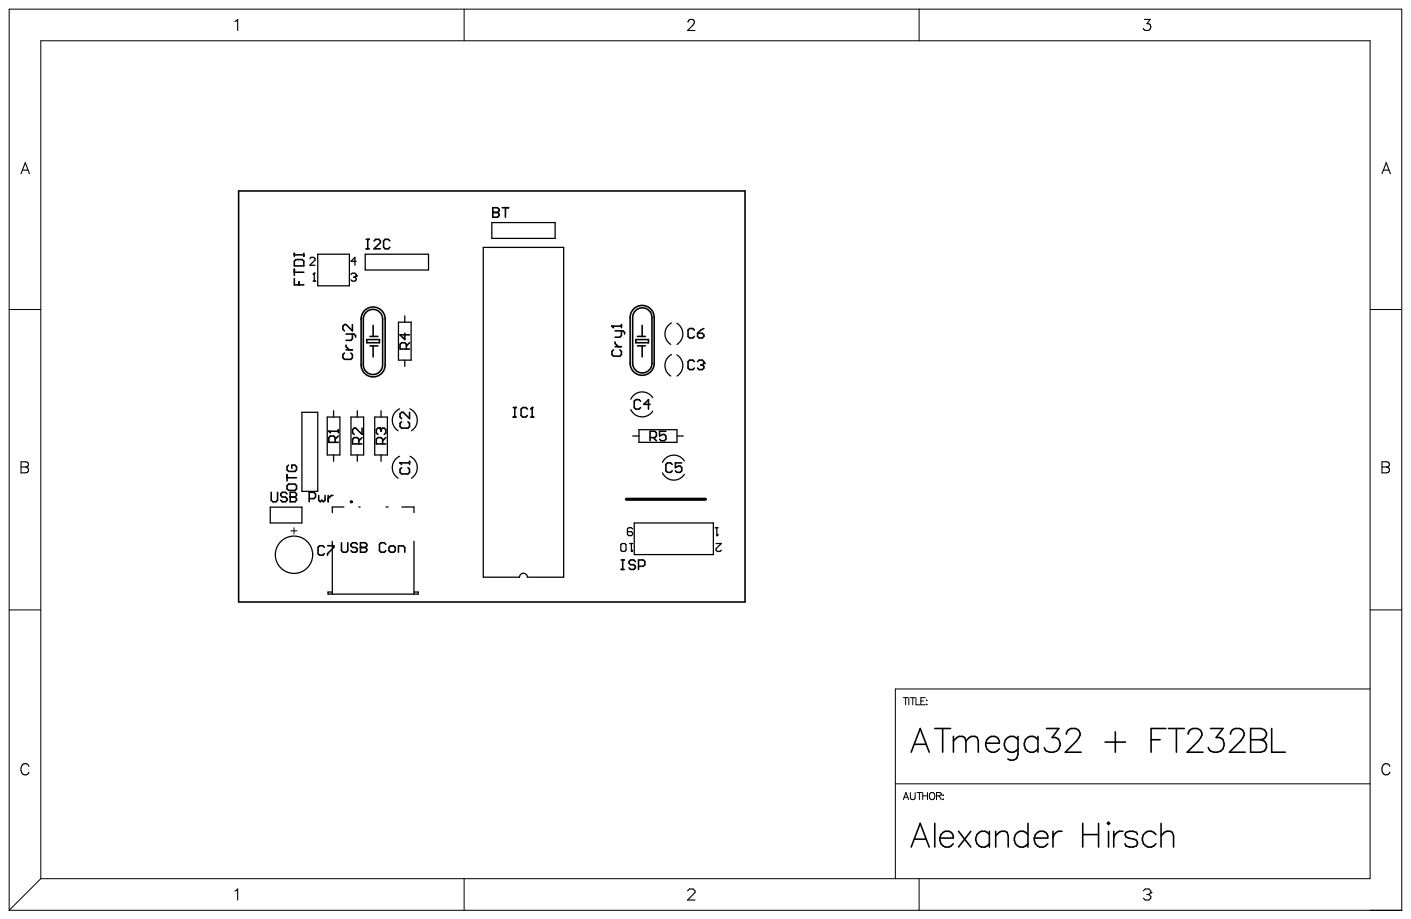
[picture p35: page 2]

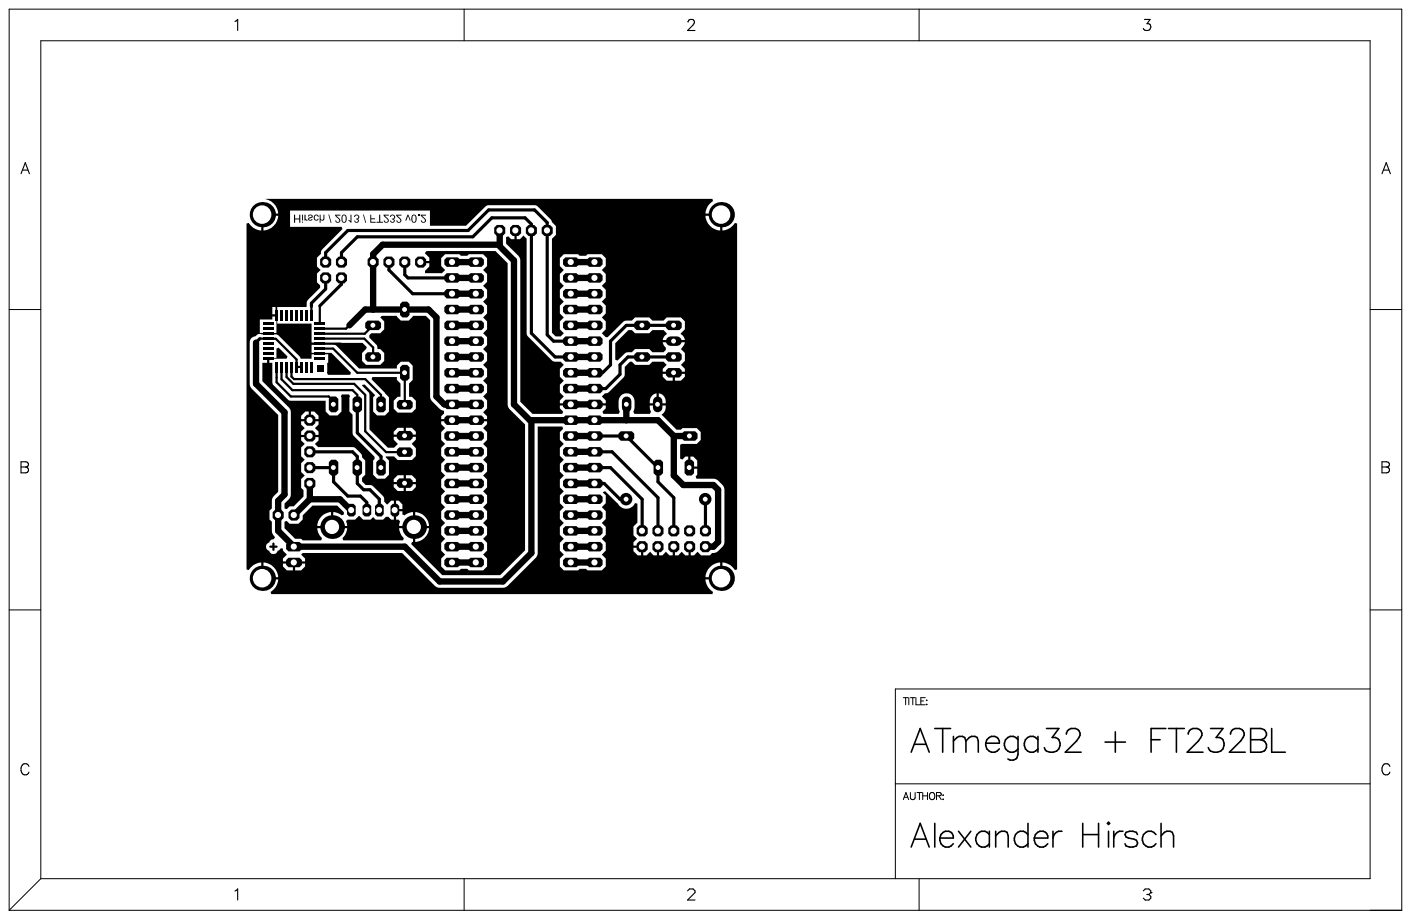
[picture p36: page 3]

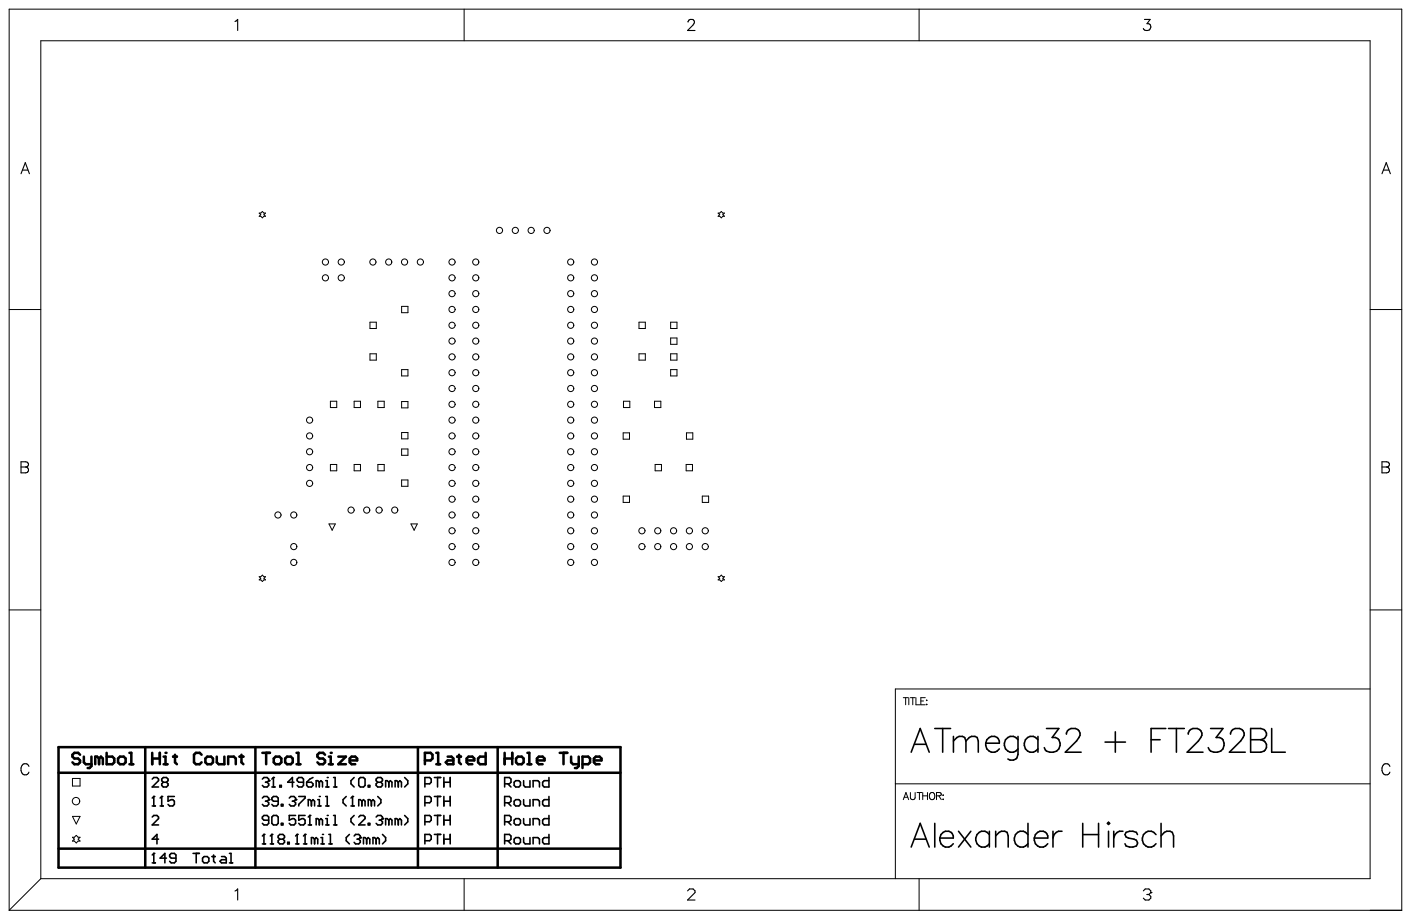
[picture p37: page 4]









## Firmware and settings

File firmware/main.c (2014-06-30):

#include "config.h"

#include <avr/io.h>
#include <avr/interrupt.h>
#include <avr/wdt.h>
#include <stdbool.h>

#include "command.h"
#include "log.h"
#include "timer1.h"
#include "twi.h"
#include "uart.h"

int main(void) {
    uart_init();
    twi_init();
    timer1_init();

    command_t *cmd = command_default();

    if(gBit(MCUCSR, 3)) {
        log("watchdog reset");
    }

    wdt_enable(WDTO_2S);

    log("init done");

    sei();

    while (true) {
        wdt_reset();

        // execute command
        if (command_get_execution_flag(cmd)) {
            cli();
            if (!command_exec(cmd)) {
                log("command not found");
            }
            command_reset(cmd);
            sei();
        }
    }

    return 0;
}

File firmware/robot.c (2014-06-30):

#include "robot.h"
#include <util/twi.h>

#include "log.h"
#include "timer1.h"
#include "twi.h"

void robot_set_velocity(int8_t left, int8_t right) {
    twi_start();
    twi_send_slave_address_write(ROBOT_SLAVE_ADDRESS);
    twi_send_byte(ROBOT_COMMAND_SET_VELOCITY);
    twi_send_byte(right);
    twi_send_byte(left);
    twi_stop();
}

void robot_set_led(uint8_t red, uint8_t blue) {
    // led values 0..63
    red >>= 2;
    blue >>= 2;

    twi_start();
    twi_send_slave_address_write(ROBOT_SLAVE_ADDRESS);
    twi_send_byte(ROBOT_COMMAND_SET_LED);
    twi_send_byte(red);
    twi_send_byte(blue);
    twi_stop();
}

void robot_drive_request(int8_t distance) {
    twi_start();
    twi_send_slave_address_write(ROBOT_SLAVE_ADDRESS);
    twi_send_byte(ROBOT_COMMAND_DRIVE_REQUEST);
    twi_send_byte(distance);
    twi_stop();
}

void robot_turn_request(int8_t angle) {
    twi_start();
    twi_send_slave_address_write(ROBOT_SLAVE_ADDRESS);
    twi_send_byte(ROBOT_COMMAND_TURN_REQUEST);
    twi_send_byte(angle);
    twi_stop();
}

void robot_get_odometry() {
    uint8_t data[6];
    uint8_t i;

    // tell slave we need odometry data
    twi_start();
    twi_send_slave_address_write(ROBOT_SLAVE_ADDRESS);
    twi_send_byte(ROBOT_COMMAND_ODOMETRY);

    // start reading
    twi_start();
    twi_send_slave_address_read(ROBOT_SLAVE_ADDRESS);
    for (i = 0; i < 5; i++) {
        data[i] = twi_receive_byte_ack();
    }
    data[5] = twi_receive_byte_nack();
    twi_stop();

    uart_printf(
            "odometry: 0x%02x 0x%02x 0x%02x 0x%02x 0x%02x 0x%02x",
            data[0],
            data[1],
            data[2],
            data[3],
            data[4],
            data[5]
            );
}

void robot_set_odometry(int8_t xlow, int8_t xheigh, int8_t ylow, int8_t
        yheigh, int8_t alphalow, int8_t alphaheigh) {
    twi_start();
    twi_send_slave_address_write(ROBOT_SLAVE_ADDRESS);
    twi_send_byte(ROBOT_COMMAND_ODOMETRY);
    twi_send_byte(xlow);
    twi_send_byte(xheigh);
    twi_send_byte(ylow);
    twi_send_byte(yheigh);
    twi_send_byte(alphalow);
    twi_send_byte(alphaheigh);
    twi_stop();
}

void robot_get_sensor(void) {
    uint8_t data[8];
    uint8_t i;

    // tell slave we need sensor data
    twi_start();
    twi_send_slave_address_write(ROBOT_SLAVE_ADDRESS);
    twi_send_byte(ROBOT_COMMAND_GET_SENSOR);

    // get sensor data (repeated start)
    twi_start();
    twi_send_slave_address_read(ROBOT_SLAVE_ADDRESS);
    for (i = 0; i < 7; i++) {
        data[i] = twi_receive_byte_ack();
    }
    data[7] = twi_receive_byte_nack();
    twi_stop();

    // redo request because of buffering

    // tell slave we need sensor data
    twi_start();
    twi_send_slave_address_write(ROBOT_SLAVE_ADDRESS);
    twi_send_byte(ROBOT_COMMAND_GET_SENSOR);

    // get sensor data (repeated start)
    twi_start();
    twi_send_slave_address_read(ROBOT_SLAVE_ADDRESS);
    for (i = 0; i < 7; i++) {
        data[i] = twi_receive_byte_ack();
    }
    data[7] = twi_receive_byte_nack();
    twi_stop();

    uart_printf(
            "sensor: 0x%02x 0x%02x 0x%02x 0x%02x 0x%02x 0x%02x 0x%02x 0x%02x",
            data[0],
            data[1],
            data[2],
            data[3],
            data[4],
            data[5],
            data[6],
            data[7]
            );
}

void robot_set_bar_level(uint8_t value) {
    value = value / (256 / (BAR_LEVEL_UP - BAR_LEVEL_DOWN));
    timer1_set_ocr(BAR_LEVEL_DOWN + value);
}

void robot_raise_bar(void) {
    uint16_t ocr = timer1_get_ocr();
    timer1_set_ocr(ocr + BAR_LEVEL_STEPS);
}

void robot_lower_bar(void) {
    uint16_t ocr = timer1_get_ocr();
    timer1_set_ocr(ocr - BAR_LEVEL_STEPS);
}

void robot_custom(uint8_t *senddata, uint8_t sendsize, uint8_t readsize) {
    // note: array will be allocated on stack
    uint8_t data[readsize];
    uint8_t i;

    // send custom data
    twi_start();
    twi_send_slave_address_write(ROBOT_SLAVE_ADDRESS);
    for (i = 0; i < sendsize; i++) {
        twi_send_byte(senddata[i]);
    }

    // receive custom data if any
    if (readsize > 0) {
        twi_start();
        twi_send_slave_address_read(ROBOT_SLAVE_ADDRESS);
        for (i = 0; i < readsize - 1; i++) {
            data[i] = twi_receive_byte_ack();
        }
        data[readsize - 1] = twi_receive_byte_nack();
    }

    twi_stop();

    // print received data if any
    if (readsize > 0) {
        uart_printf_nole("custom: ");
        for (i = 0; i < readsize; i++) {
            uart_printf_nole("0x%02x", data[i]);
            if (i < readsize - 1) {
                uart_printf_nole(" ");
            }
        }
        // send default lineending
        uart_printf("");
    }
}
